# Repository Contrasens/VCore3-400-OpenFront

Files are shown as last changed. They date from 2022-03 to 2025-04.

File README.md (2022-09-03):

# VCore3.0 400mm OpenFront

This is my take at the VCore-3 3D printer from RatRig.

It contains several mods already, the basis is the 400mm VCore-3 from RatRig [https://www.ratrig.com/3d-printing-cnc/3d-printer-kits/all-3d-printer-kits/v-core3configurable.html](https://www.ratrig.com/3d-printing-cnc/3d-printer-kits/all-3d-printer-kits/v-core3configurable.html). The mods I decided to build are: 

* OpenFront Mod: [https://www.thingiverse.com/thing:5140728](https://www.thingiverse.com/thing:5140728)
* Various smaller mods from users of the RatRig community (many thanks to everybody making this great 3D printer an even better one!):
  * [RatRig V-Core 3 Bed Arms heat-set insert mod](https://www.prusaprinters.org/prints/145226-ratrig-v-core-3-bed-arms-heat-set-insert-mod)
  * [RatRig V-Core 3 reinforced and sealed rear motor mount](https://www.printables.com/model/158467-ratrig-v-core-3-reinforced-and-sealed-rear-motor-m)
  * Stronger Pillow Blocks
  * [LGX Lite Fast-Swap-Rigid Gold Series EVA mod](https://www.thingiverse.com/thing:5207408)
  * [Gold Series Rat Rig V-Core 3, XY joiners with clamping mod](https://www.thingiverse.com/thing:4947482)
* ...and my own mods:
  * [My Enclosure](https://www.printables.com/model/270834-enclosure-for-my-ratrig-v-core3-400mm-openfront)
  * [Magnetic holder for PC/Acrylic panels](https://www.printables.com/model/229334-magnetic-holder-for-pcacrylic-panels)
  * [DIN Rail Endcaps for M6x12 Cap Screws](https://www.printables.com/model/152627-din-rail-endcaps-for-m6x12-cap-screws)
  * [DIN Rail Adapter for Meanwell RS-25-5](https://www.printables.com/model/152624-din-rail-adapter-for-meanwell-rs-25-5)
  * [DIN Rail Adapter for Meanwell LRS-200-24 for V-Core3 400](https://www.printables.com/model/152620-din-rail-adapter-for-meanwell-lrs-200-24-for-v-cor)
  * [Fastener for Igus Chain on VCore3](https://www.printables.com/model/145317-fastener-for-igus-chain-on-vcore3)

## How it looks
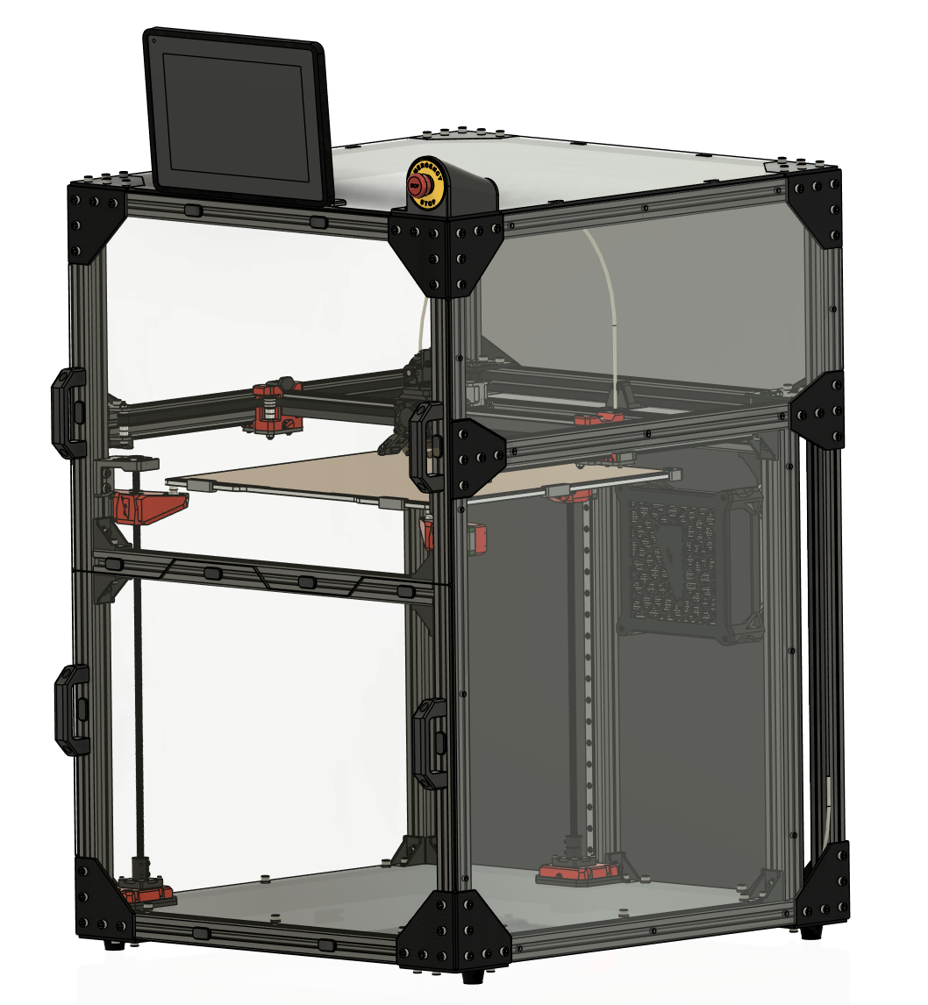
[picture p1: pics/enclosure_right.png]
Enclosure

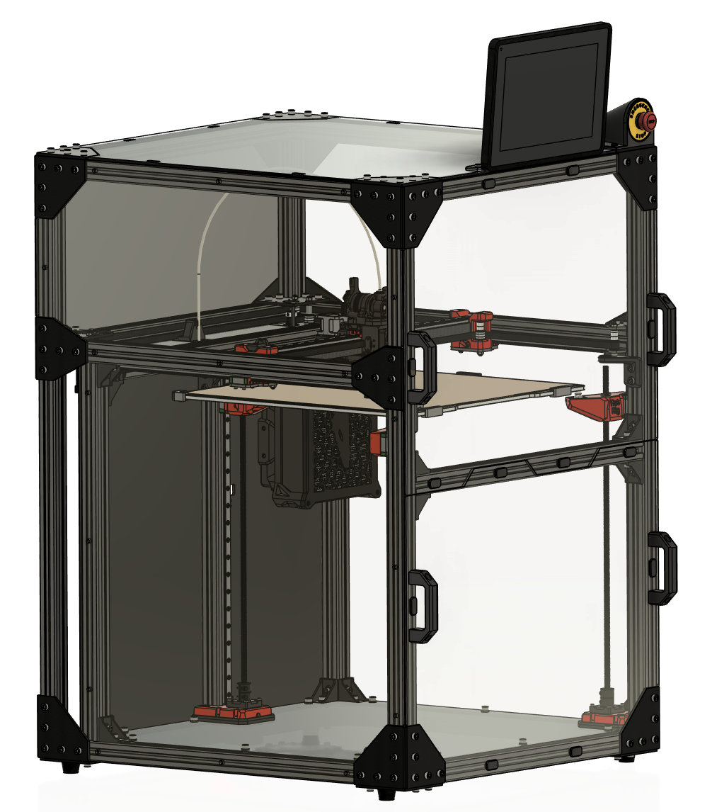
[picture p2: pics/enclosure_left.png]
Enclosure

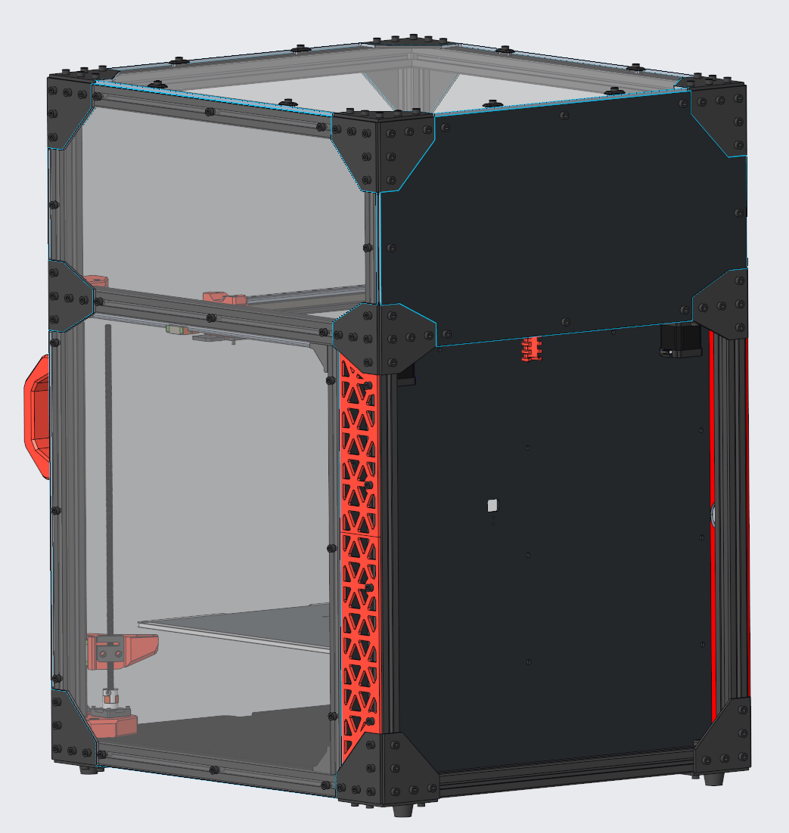
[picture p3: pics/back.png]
Back View

Here is the wiring diagram I will be using. **If you decide to use it, please acknowledge that you are doing this on your own risk!**
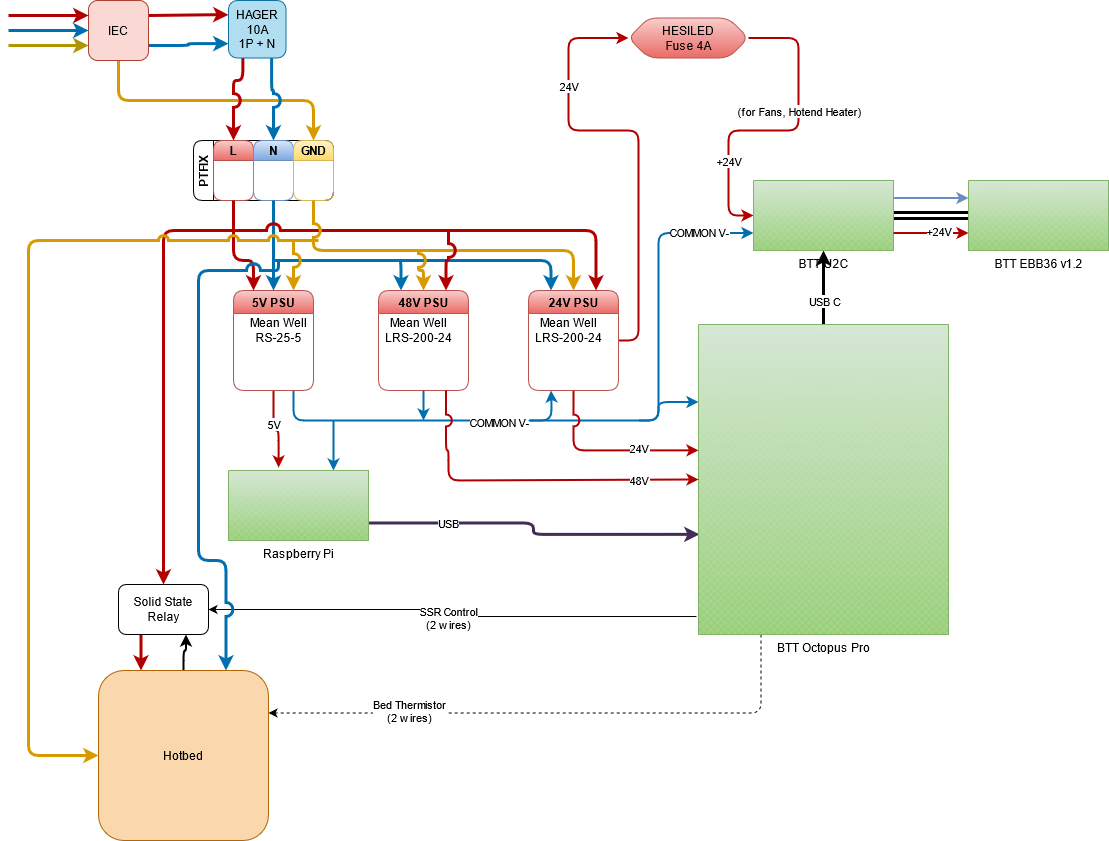
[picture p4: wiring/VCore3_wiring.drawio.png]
Wiring


## Printhead
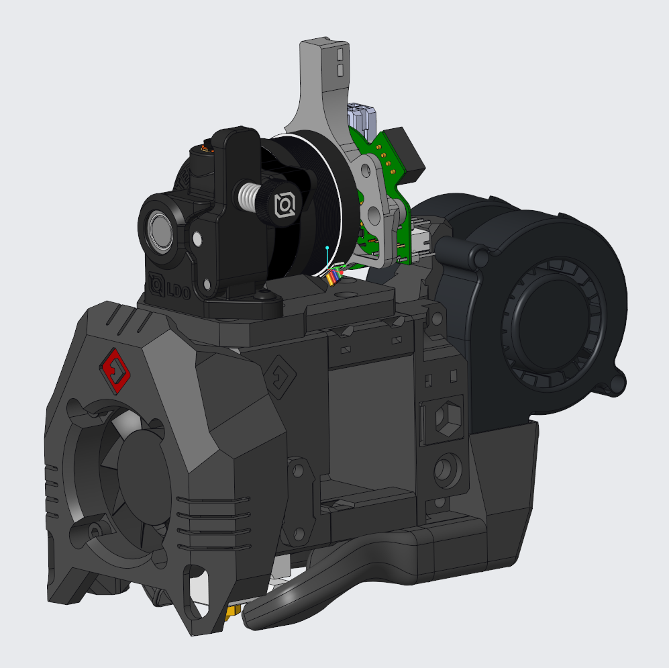
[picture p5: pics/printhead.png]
Printhead


## BOM
Here is my Bill of Material (BOM): [GoogleDrive](https://docs.google.com/spreadsheets/d/1t07DfJ-j9_pQZ918qX5IQbVI45c6goUu2t6Ui3eUhBY/edit?usp=sharing)

## Contact
* [Discord](https://discord.com) user: [Dinu#6139](http://discordapp.com/users/704373657648234526)

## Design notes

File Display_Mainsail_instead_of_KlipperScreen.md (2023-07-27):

# How to switch from using KlipperScreen to Mainsail on the HDMI output of the Raspberry Pi?

## Stop and disable KlipperScreen service
  ```
  sudo systemctl stop KlipperScreen
  sudo systemctl disable KlipperScreen
  ```

## Install Chromium and use the page served by Mainsail in kiosk mode
Read the guidelines (German) available here: [Kiosk Modus auf Touchscreen am Raspberry Pi mit automatischer Anmeldung im Browser](https://smarthomeyourself.de/wiki/raspberrypi/kiosk-modus-auf-touchscreen-am-raspberry-pi-mit-automatischer-anmeldung-im-browser). Basically, you need to do the following (I am just summarizing the steps from the link for future reference in case the content will disappear):

### Raspi Setup 
Disable Overscan compensation
  
  ```
  sudo raspi-config
  2 - Display Options -> D2 - Underscan =>> NO (DISABLE overscan compensation)
  ```
Enable Auto-login
  ```
  sudo raspi-config
  1 - System Options -> S5 – Boot / Auto Login =>> B2 – Console Autologin
  ```

### Install Necessary Packets
Update Raspbian
```
sudo apt update
sudo apt upgrade
```
Install X11 server and the Chromium browser
```
sudo apt-get install --no-install-recommends xserver-xorg x11-xserver-utils xinit openbox xdotool
sudo apt-get install --no-install-recommends chromium-browser
```

### Configure Autostart
```
sudo nano /etc/xdg/openbox/autostart
```
In the file, add the following (when finished, close & save with Ctrl+X):
```
xset -dpms            # turn off display power management system
xset s noblank        # turn off screen blanking
xset s off            # turn off screen saver

# Remove exit errors from the config files that could trigger a warning
sed -i 's/"exited_cleanly":false/"exited_cleanly":true/' ~/.config/chromium/'Local State'
sed -i 's/"exited_cleanly":false/"exited_cleanly":true/; s/"exit_type":"[^"]\+"/"exit_type":"Normal"/' ~/.config/chromium/Default/Preferences

# Run Chromium in kiosk mode
chromium-browser  --noerrdialogs --check-for-update-interval=31536000 --disable-infobars --kiosk $KIOSK_URL &
```

### Set the Home Address to be opened in the Browser
```
sudo nano /etc/xdg/openbox/environment
```
In the file, add the following (when finished, close & save with Ctrl+X):
```
  export KIOSK_URL=http://127.0.0.1
```

### Start xserver (without showing the cursor)
```
sudo nano ~/.bash_profile
```
In the file, add the following (when finished, close & save with Ctrl+X):
```
[[ -z $DISPLAY && $XDG_VTNR -eq 1 ]] && startx -- -nocursor
```

### Automatically login into the browser after boot
```
sudo nano /etc/xdg/openbox/autostart
```
Add the following at the end of the file (when finished, close & save with Ctrl+X):
```
sleep 30
exec /home/pi/start_ha.sh
```
Now, create the start_ha.sh file (a shell script):
```
sudo nano /home/pi/start_mainsail.sh
```
In the file, add the following (when finished, close & save with Ctrl+X):
```
# login to Mainsail (not necessary?)
sleep 30
export XAUTHORITY=/home/pi/.Xauthority; export DISPLAY=:0; xdotool type YOUR_MAINSAIL_USERNAME
sleep 1;
export XAUTHORITY=/home/pi/.Xauthority; export DISPLAY=:0; xdotool key Tab
sleep 1;
export XAUTHORITY=/home/pi/.Xauthority; export DISPLAY=:0; xdotool type YOUR_MAINSAIL_PASSWORD

sleep 1;
export XAUTHORITY=/home/pi/.Xauthority; export DISPLAY=:0; xdotool key Return
sleep 5;

# click save login-button
export XAUTHORITY=/home/pi/.Xauthority; export DISPLAY=:0; xdotool mousemove 1835 1030;
sleep 1;
export XAUTHORITY=/home/pi/.Xauthority; export DISPLAY=:0;xdotool click 1;
sleep 2;
```
Change the rights of the newly created file to be executable:
```
sudo chmod +x /home/pi/start_ha.sh
```
Reboot, and enjoy!
```
sudo reboot now
```

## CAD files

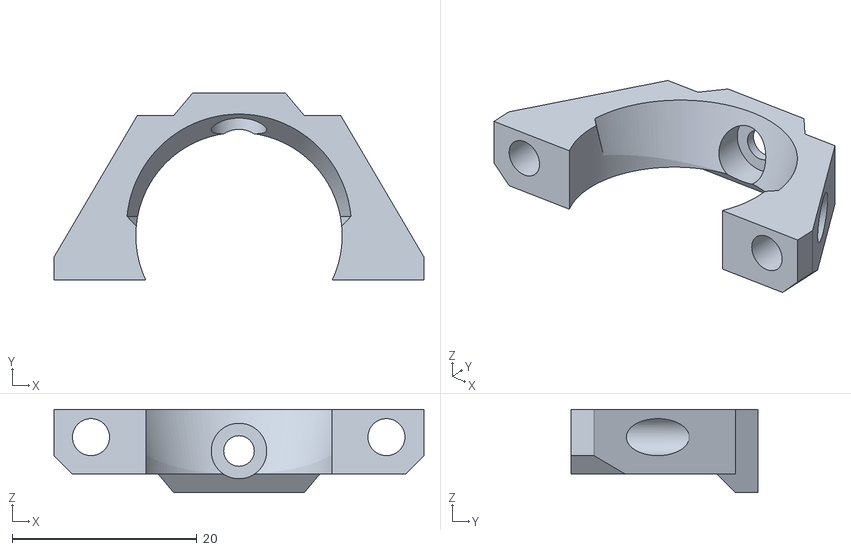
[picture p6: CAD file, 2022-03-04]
cad/_PRINTED_/EVA2.4.0/black/Dragon_heatsink_support.stl
40.0 x 20.2 x 9.00

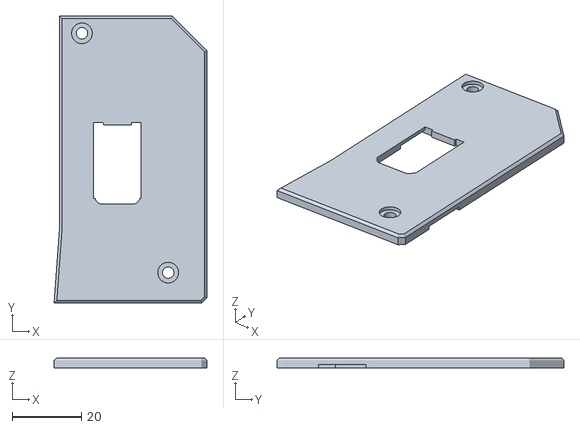
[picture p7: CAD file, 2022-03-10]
cad/_PRINTED_/extra/black/sabre_holder_top.stl
44.2 x 83.0 x 3.00

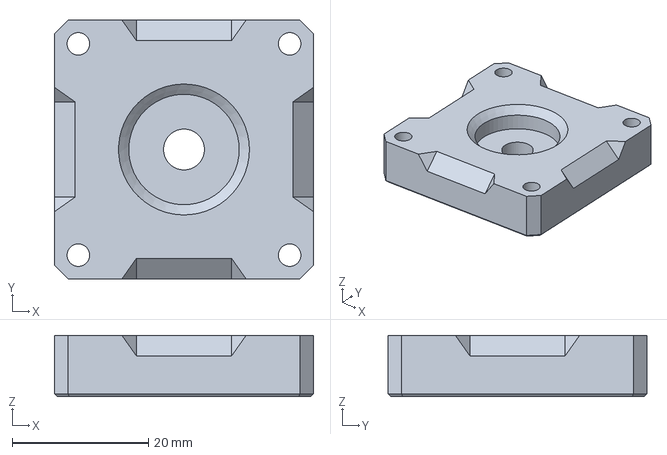
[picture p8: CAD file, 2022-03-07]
cad/_PRINTED_/printed_parts/essentials/black/pillow_block_lower.step
38.0 x 38.0 x 9.00 mm

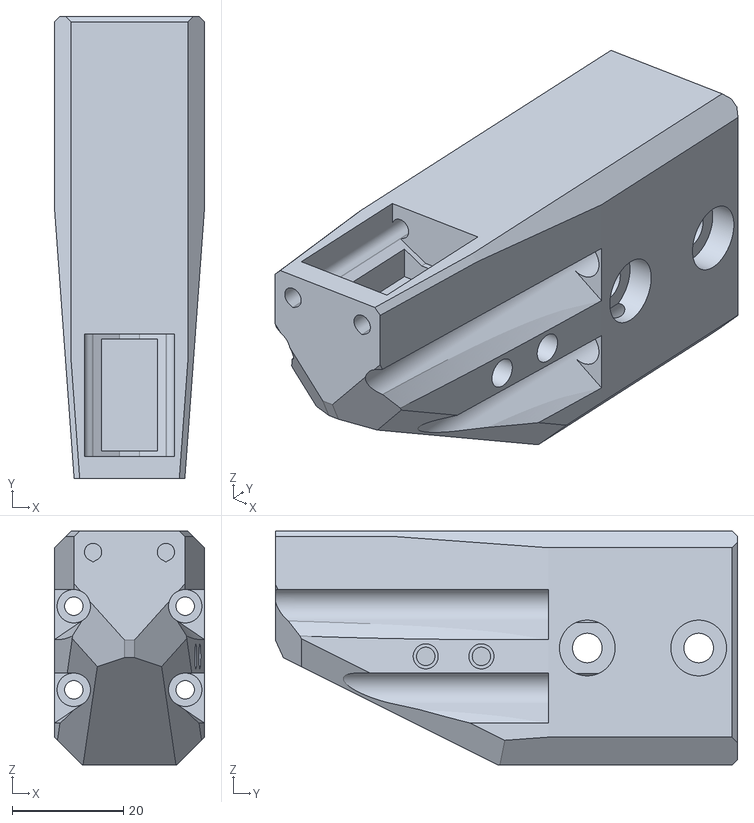
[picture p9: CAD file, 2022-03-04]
cad/_PRINTED_/printed_parts/essentials/red/V-Core-heat-inset_bed_arm_back.stl
27.0 x 83.0 x 42.0

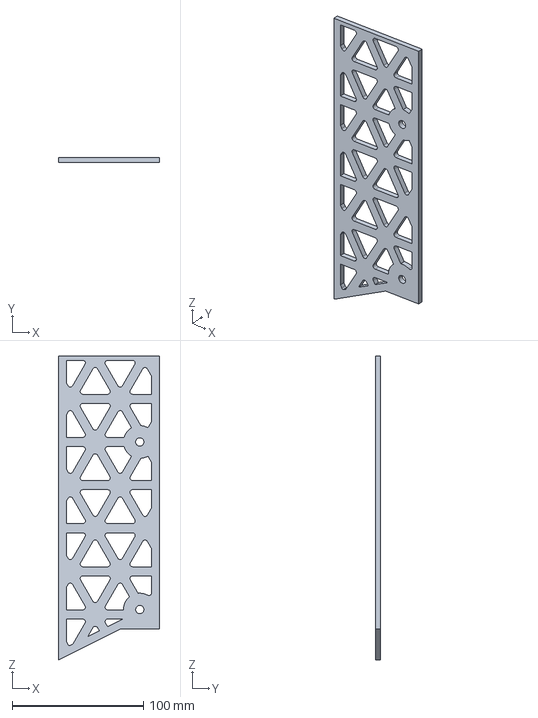
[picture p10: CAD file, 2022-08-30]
cad/Enclosure/Meshes/side_mesh_right_top.stp
77.0 x 4.00 x 232.0 mm

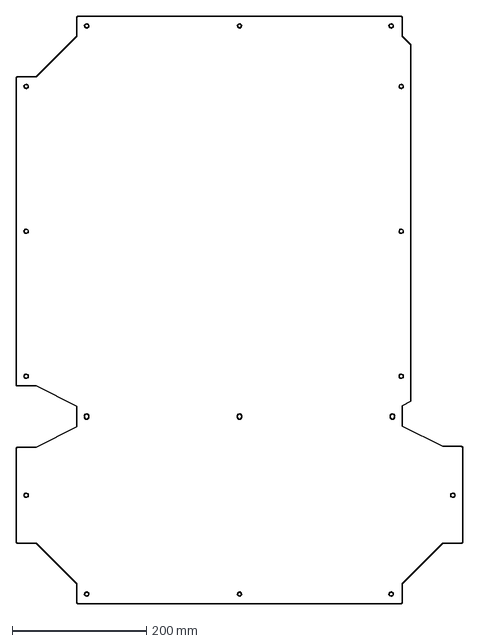
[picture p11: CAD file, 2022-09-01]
cad/Enclosure/Panels/DXF/side-panel_PC4mm_2X.dxf
664.0 x 874.0 mm

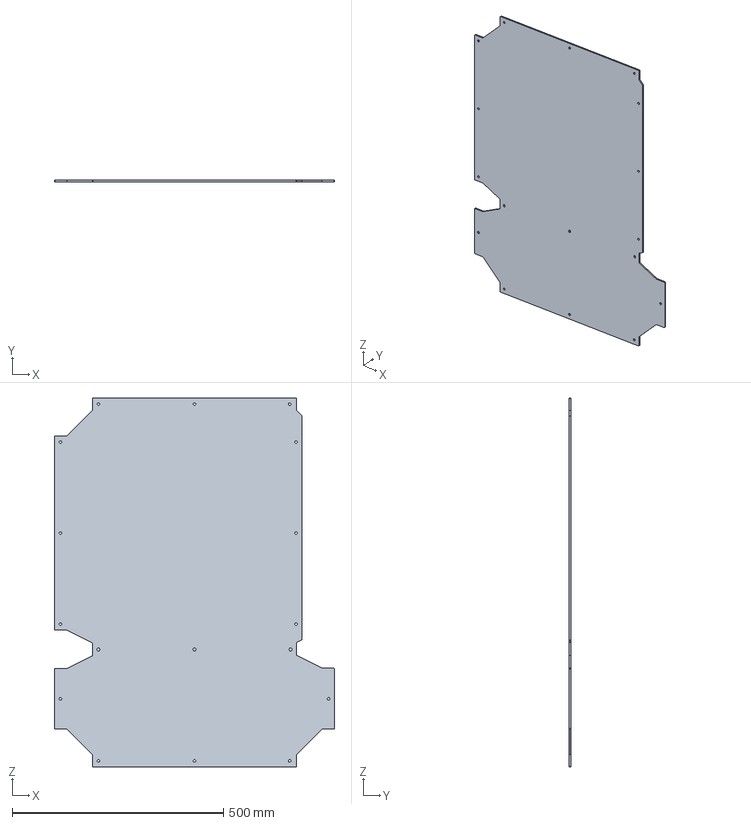
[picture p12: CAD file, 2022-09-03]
cad/Enclosure/Panels/STEP/side-panel.stp
664.0 x 4.00 x 874.0 mm

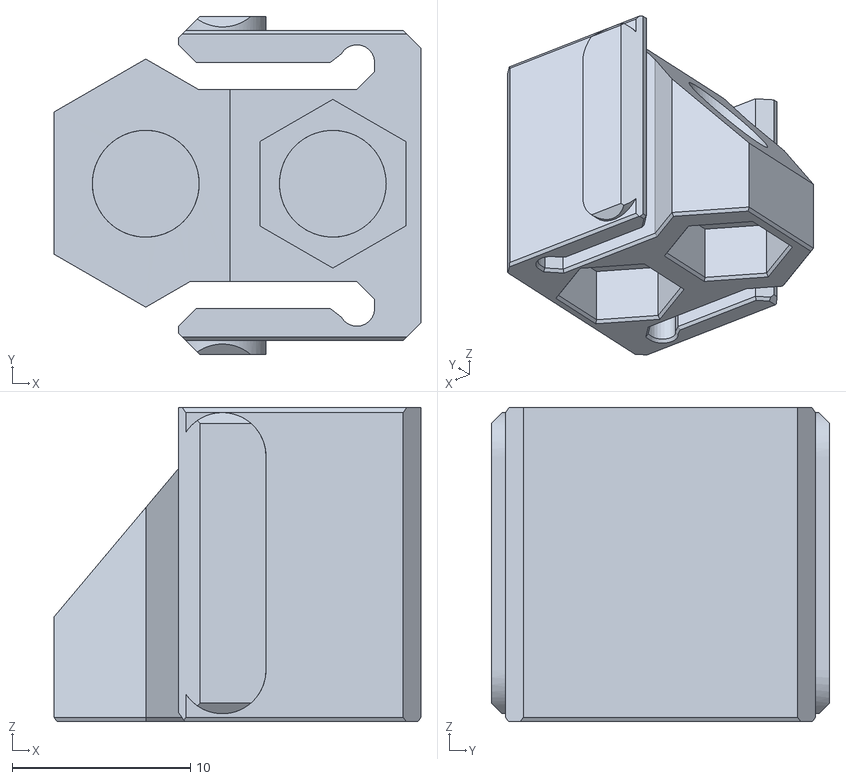
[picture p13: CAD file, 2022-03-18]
cad/Extras/Carbon Tube Adapter/x-tube_nuts.stl
20.6 x 19.0 x 17.6

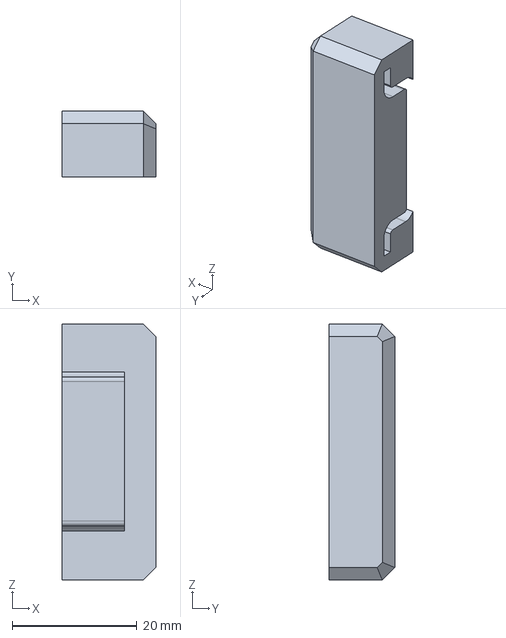
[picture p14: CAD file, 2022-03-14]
cad/Extras/DIN Rail Adapters/DIN Rail Endcaps/din_rail-end.stp
15.0 x 10.5 x 41.0 mm

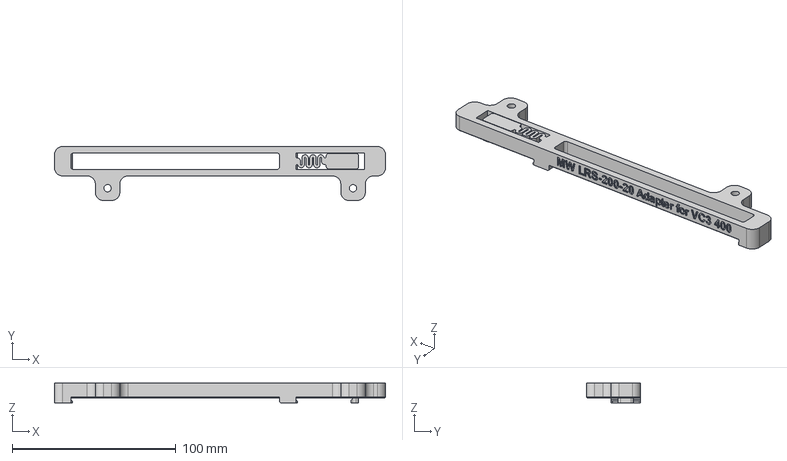
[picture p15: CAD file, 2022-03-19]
cad/Extras/DIN Rail Adapters/MeanWell LRS-200-24/lrs-200-24_din_adapter_v3.step
202.3 x 33.0 x 12.0 mm

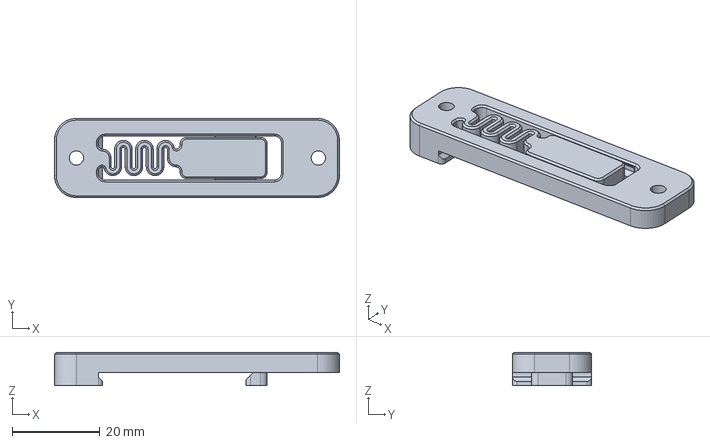
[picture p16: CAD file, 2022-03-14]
cad/Extras/DIN Rail Adapters/MeanWell RS-25-5/rs-25-5_din_adapter.stp
64.8 x 18.0 x 7.60 mm

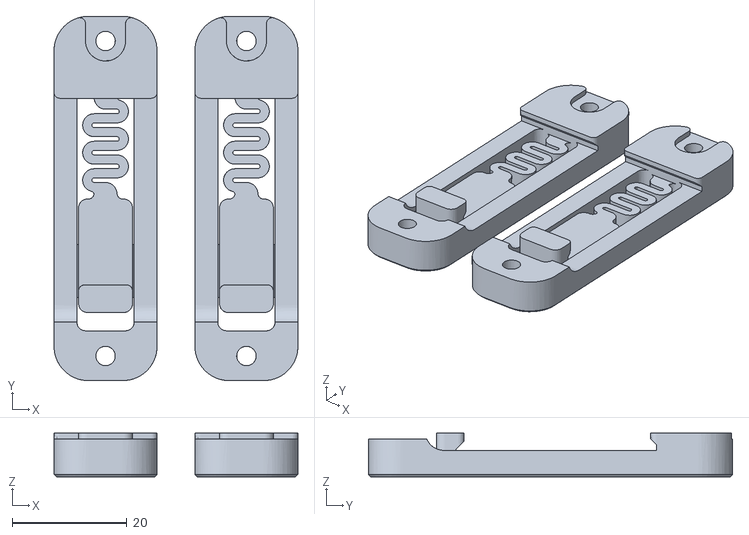
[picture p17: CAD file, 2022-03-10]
cad/Extras/DIN Rail Adapters/Octopus_Raspi_mount/DIN_Support_X2.stl
42.6 x 63.6 x 7.60

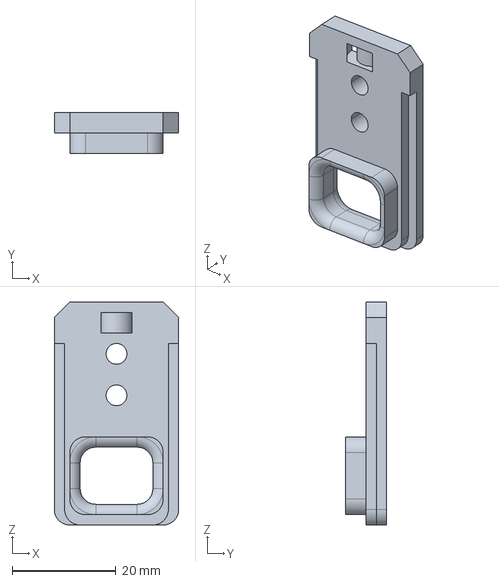
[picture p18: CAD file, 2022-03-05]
cad/Extras/Igus Chain/befestigung_igus_kette.stp
24.0 x 8.00 x 43.0 mm

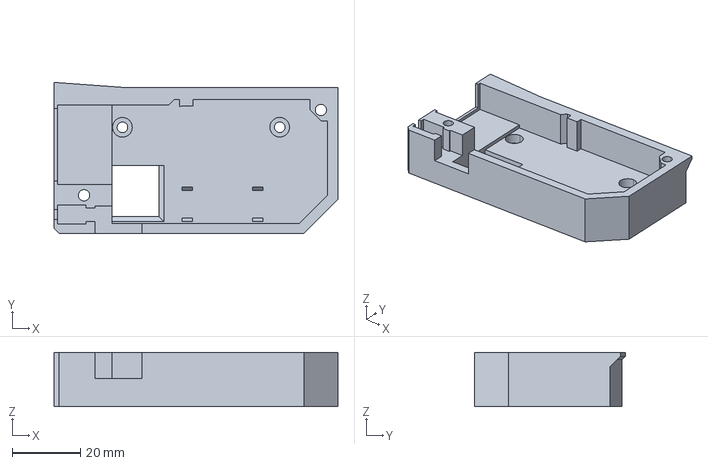
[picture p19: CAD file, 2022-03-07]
cad/Extras/Igus Chain/Jevermeister/sabre_holder.stp
83.0 x 44.2 x 15.8 mm

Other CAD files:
cad/Mods/EVA_2_4_0_LGXLite_Dragon_Inserts/[Face] Universal - universal_face.stl
cad/Mods/EVA_2_4_0_LGXLite_Dragon_Inserts/Addons/top_endstop_angled.stl
cad/Mods/Jevermeister/Bed Arms Heat Inserts/V-Core-heat-inset_bed_arm_back.step
cad/Mods/Jevermeister/EVA Toolboard Holder/eva_toolboard_cable_relief v1.stl
MM_Prints/RR_Disk.3mf
My_SS_Profiles/ratrig-vcore-bed-400x400.stl
cad/Enclosure/Accesories/3030_handle.stp
cad/Enclosure/Accesories/magnet_holder_1_magnet.step
cad/Enclosure/Accesories/magnet_holder_2_magnets.step
cad/Enclosure/Accesories/screw_holder.stp
cad/Enclosure/Meshes/side_mesh_right_bottom.stp
cad/Enclosure/Panels/DXF/back-panel_DIBOND.dxf
cad/Enclosure/Panels/DXF/front-panel_PC4mm.dxf
cad/Enclosure/Panels/DXF/side-panel_PC4_2X.dxf
cad/Enclosure/Panels/DXF/side-panel_X2_PC4mm.dxf
cad/Enclosure/Panels/DXF/top-panel_PC4mm.dxf
cad/Enclosure/Panels/STEP/back-panel.stp
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

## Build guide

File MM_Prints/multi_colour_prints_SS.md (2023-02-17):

# How to set-up SuperSlicer to work with multi-colour material

## Prerequisites
- SuperSlicer (tested with: v2.4.58.4, v2.4.58.5, v2.5.59.0 and nightly v2.5.59.2)
- Expert settings enabled

## HowTo Step-by-step
1. Printer Settings 
   - General -> Capabilities -> Extruders = 2
   - General -> Capabilities -> Single Extruder Multi Material = True
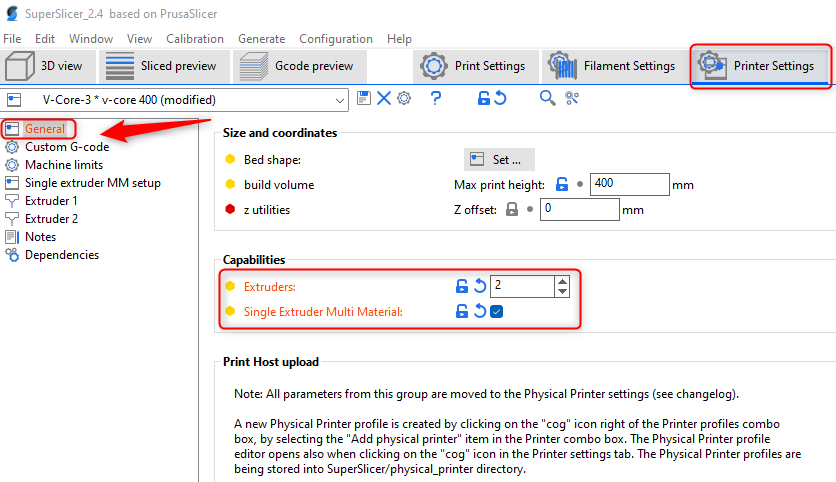
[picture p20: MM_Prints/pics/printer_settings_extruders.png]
Printer Settings
 

1. **Save & Restart SuperSlicer**
 
2. Printer Settings, set all Single extruder multimaterial parameters to 0:
   
   - General -> Use relative E distances = enable
   - Custom G-code -> Tool change g-code: add "PAUSE" (without the ")
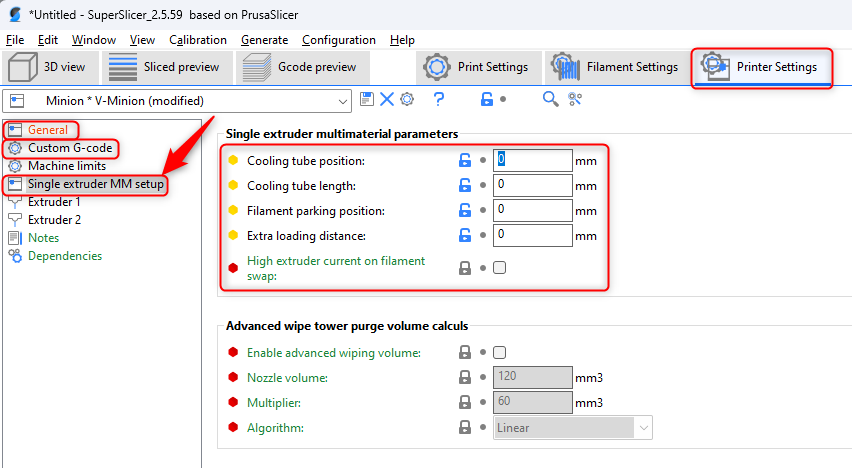
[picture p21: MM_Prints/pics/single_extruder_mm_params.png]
Single Extruder
 

 1. Filament settings
      - Multimaterial settings -> Wipe tower parameters -> Minimal purge on wipe tower = 200 for V6 and 500 for Volcano
      - Multimaterial settings -> Wipe tower parameters -> Max speed on the wipe tower = 300%
      - Multimaterial settings -> Toolchange parameters with single extruder MM printers -> Number of cooling moves = 0
      - Multimaterial settings -> Toolchange parameters with single extruder MM printers -> Ramming parameters
        - Turn off all Ramming settings:
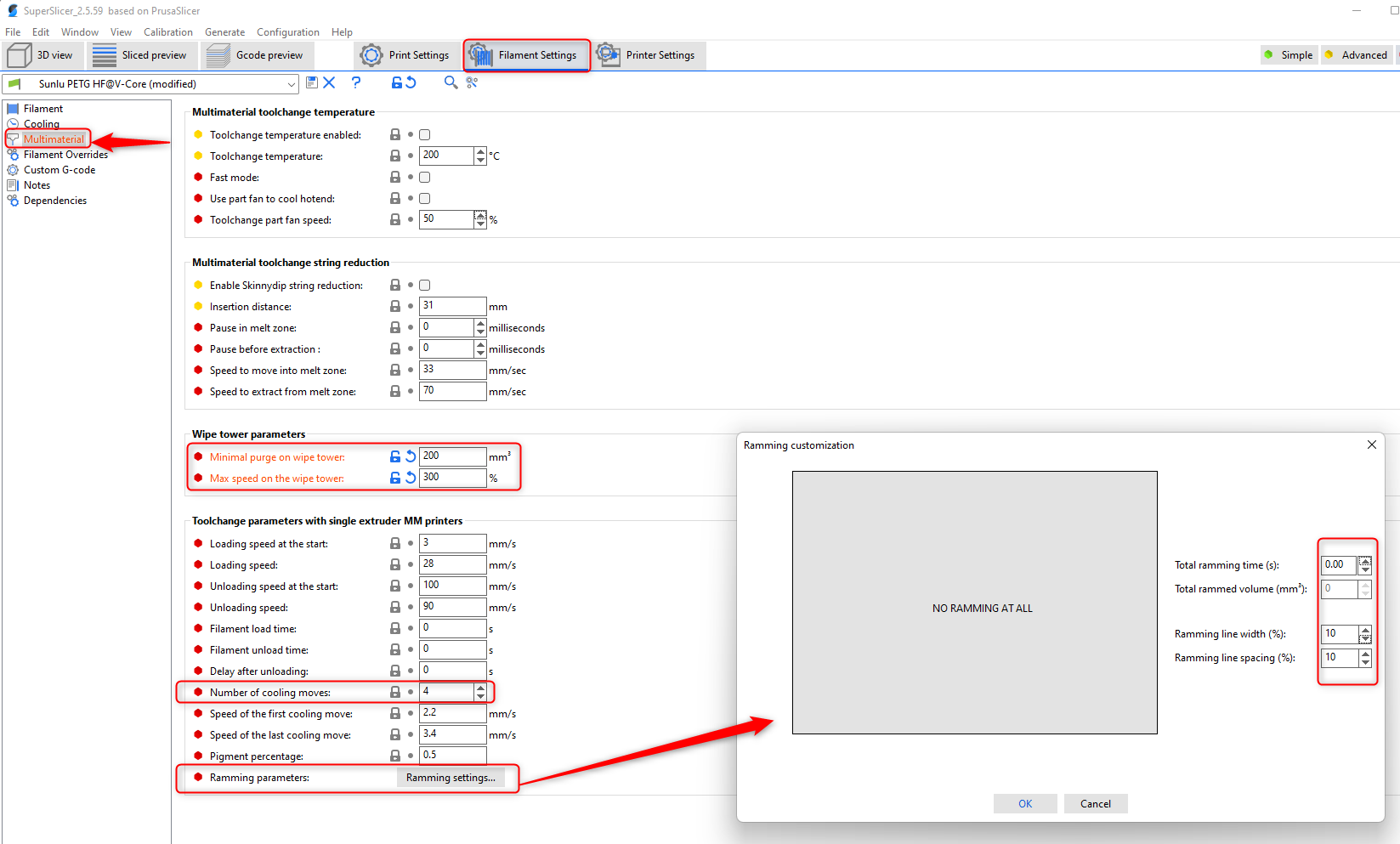
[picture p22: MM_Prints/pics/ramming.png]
Deactivate ramming
          
 2. Print settings
      - Multiple extruders -> wipe tower = enable
      - Multiple extruders -> wipe tower -> "Prime all printing extruders" is not set
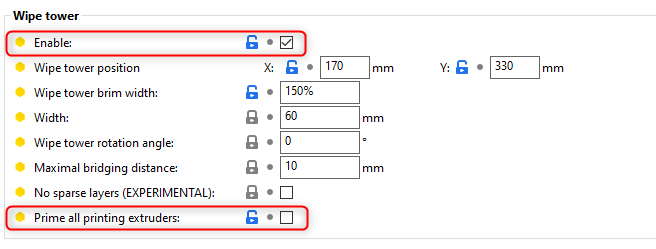
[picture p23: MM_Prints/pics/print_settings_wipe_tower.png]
Wipe Tower settings
        

## How to slice the objects with different colours
- The object that need to be printed in several colours must be made out of several smaller objects, for each colour a separate one, so first split the object
- Import all of the objects in SuperSlicer: first the base object, then right click it -> Add part -> Load
  
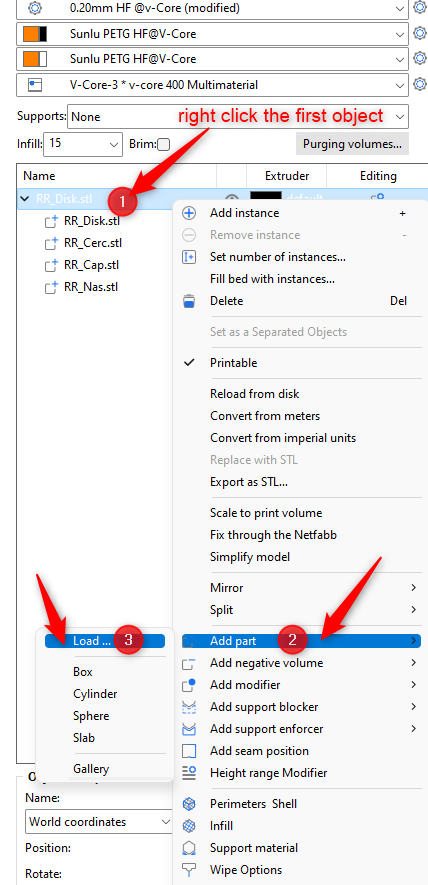
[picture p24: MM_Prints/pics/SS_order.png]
SS Order
  
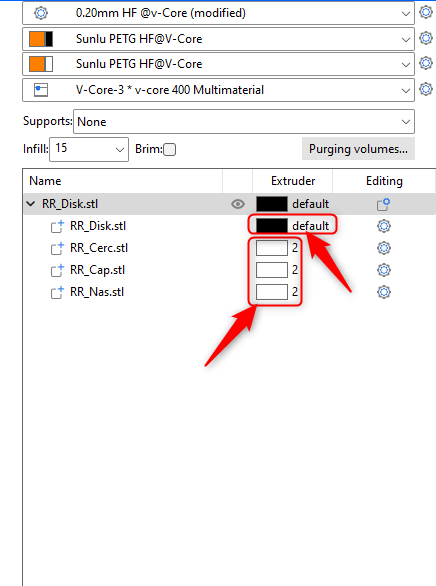
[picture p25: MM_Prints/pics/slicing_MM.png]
Slicing
  
  
- Associate them with different extruders
- Slice it and start the print
- When the print pauses, swap the filament and then click resume

## Example 
You can use this example SS Project: [RR_Disk.3mf](RR_Disk.3mf)

## Special Thanks:
Helge Keck for writing the initial version for the RatRig Discord Community

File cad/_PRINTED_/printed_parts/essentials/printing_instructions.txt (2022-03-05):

https://v-core.ratrig.com/printed_parts/#printing-instructions

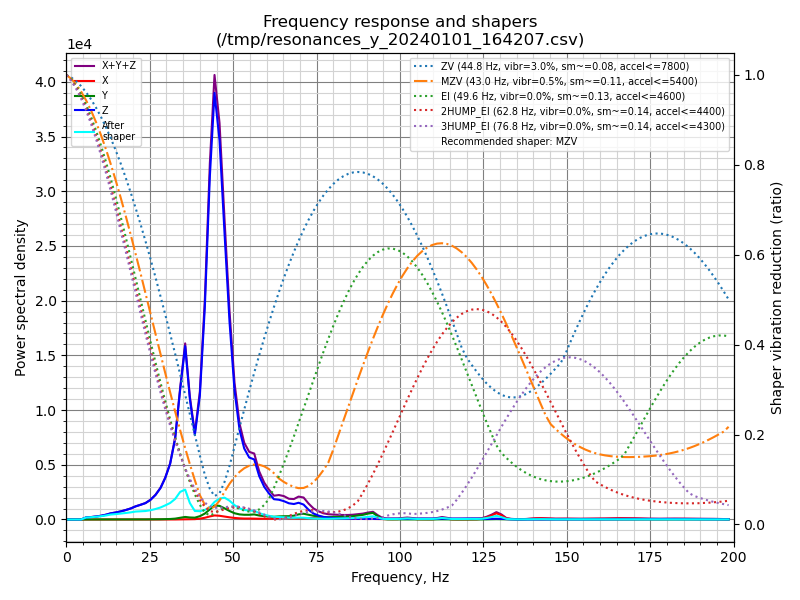
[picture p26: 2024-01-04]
printer_data/ratos_2_0_config/input_shaper/resonances_y_2024-01-01-164435.png

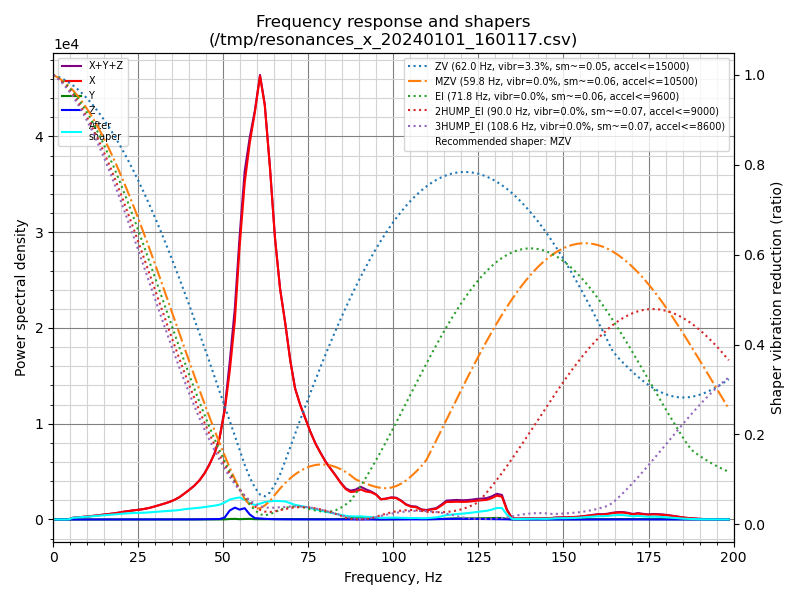
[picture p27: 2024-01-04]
printer_data/ratos_2_0_config/input_shaper/resonances_x_2024-01-01-160543.png

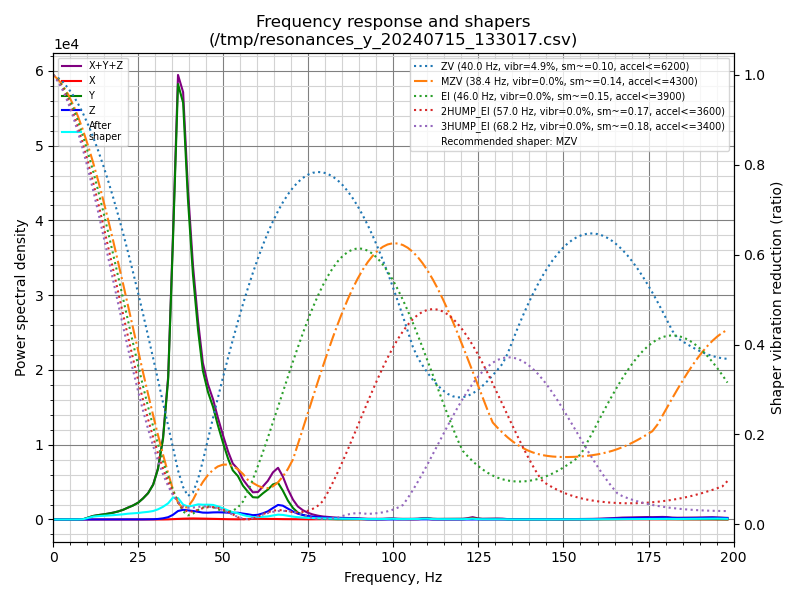
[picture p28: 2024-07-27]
printer_data/ratos_2_1_config/input_shaper/input_shaper/resonances_y_2024-07-15-133238.png

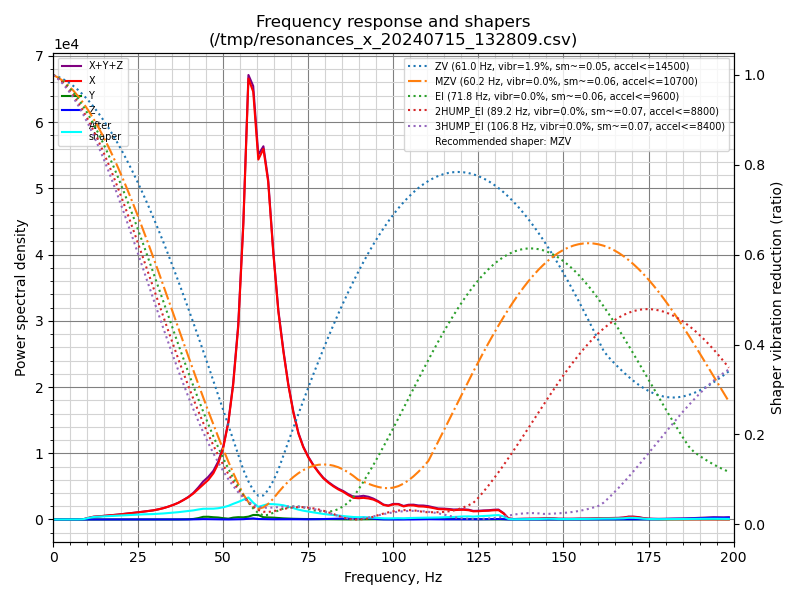
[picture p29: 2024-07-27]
printer_data/ratos_2_1_config/input_shaper/input_shaper/resonances_x_2024-07-15-133224.png

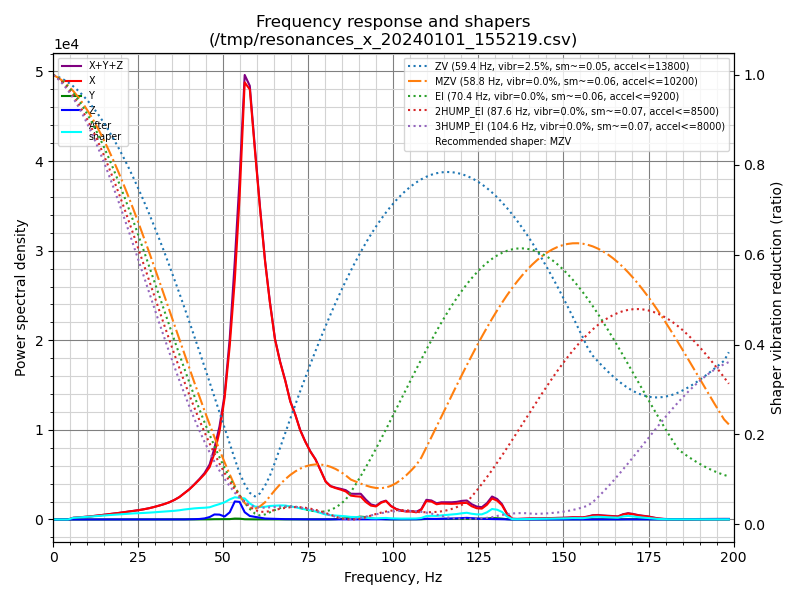
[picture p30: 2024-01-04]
printer_data/ratos_2_0_config/input_shaper/resonances_x_2024-01-01-155646.png

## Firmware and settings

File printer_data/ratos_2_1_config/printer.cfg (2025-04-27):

#############################################################################################################
### CONFIGURATION GENERATED BY THE RATOS CONFIGURATOR
#############################################################################################################
#[include RatOS.cfg]  # this is the unmodified RaatOS configuration
[include RatOS_modified.cfg]

#############################################################################################################
### MACRO CONFIGURATION
### Configure the behavior of RatOS macros
### See: https://os.ratrig.com/docs/configuration/macros
#############################################################################################################
[gcode_macro RatOS]
variable_relative_extrusion: False
variable_preheat_extruder: True
variable_calibrate_bed_mesh: True
variable_nozzle_priming: "primeblob"
variable_start_print_park_in: "back"
variable_start_print_park_z_height: 50
variable_end_print_park_in: "back"
variable_pause_print_park_in: "back"
variable_macro_travel_speed: 600
variable_macro_travel_accel: 8000
# Euclid macros
variable_stowable_probe_position_preflight: [ 27, 30 ]
variable_stowable_probe_position_side:      [ 27, 0  ]
variable_stowable_probe_position_dock:      [  7, 0  ]
variable_stowable_probe_position_exit:      [  7, 30 ]
# Adaptive meshing
variable_adaptive_mesh: True

#############################################################################################################
### USER OVERRIDES & CUSTOM CONFIGURATION
### Anything custom you want to add, or RatOS configuration you want to override, do it here.
### This section is pre-populated with the most common settings you may want to change.
### See: https://os.ratrig.com/docs/configuration/includes-and-overrides
###
### It is recommended that you follow these steps to properly calibrate your printer:
### 0) Sanity check and PID Tuning: https://www.klipper3d.org/Config_checks.html
### 1) Z-offset calibration: https://www.klipper3d.org/Probe_Calibrate.html#calibrating-probe-z-offset
### 2) Pressure Advance: https://www.klipper3d.org/Pressure_Advance.html
### 3) Skew Correction: https://www.klipper3d.org/Skew_Correction.html
### 4) Resonance Compensation: https://www.klipper3d.org/Resonance_Compensation.html
### RatOS has dedicated macro's to generate shaper graphs for deeper analysis (requires accelerometer).
### Use MEASURE_COREXY_BELT_TENSION to compare tension between belts, and use
### GENERATE_SHAPER_GRAPHS to generate the resonance graphs for analysing and manually entering input shaper
### configuration.
### You can run SHAPER_CALIBRATE to automatically calibrate your input shaper configuration, if you just want
### to get started.
### Additionally, you can use the Realtime Analysis Tool to analyze your printer's performance in real-time.
### Read more about klipper here: https://www.klipper3d.org/Overview.html
#############################################################################################################

#---------------------------------------------------- X -----------------------------------------------------
# The A motor in the CoreXY system, located at the rear left of the printer
# Connected to MOTOR 0 on Octopus Pro 446
#------------------------------------------------------------------------------------------------------------
[stepper_x]
dir_pin: !x_dir_pin                 # Add ! in front of pin name to reverse the direction of stepper_x
rotation_distance: 40              # 40 for 20 tooth 2GT pulleys, 32 for 16 tooth 2GT pulleys
homing_speed: 50
position_min: 0
position_max: 400
position_endstop: 0

#---------------------------------------------------- Y -----------------------------------------------------
# The B motor in the CoreXY system, located at the rear right of the printer
# Connected to MOTOR 1 on Octopus Pro 446
#------------------------------------------------------------------------------------------------------------
[stepper_y]
dir_pin: !y_dir_pin                 # Add ! in front of pin name to reverse the direction of stepper_y
rotation_distance: 40              # 40 for 20 tooth 2GT pulleys, 32 for 16 tooth 2GT pulleys
homing_speed: 50
position_min: 0
position_max: 400
position_endstop: 400

#---------------------------------------------------- Z -----------------------------------------------------
# The left Z motor for the kinematic bed
# Connected to MOTOR 5 on Octopus Pro 446
#------------------------------------------------------------------------------------------------------------
[stepper_z]
dir_pin: !z0_dir_pin               # Remove ! in front of pin name to reverse the direction of stepper_z
rotation_distance: 4               # 4 for TR8*4 lead screws
homing_speed: 10
position_min: -5
position_max: 400

#---------------------------------------------------- Z1 ----------------------------------------------------
# The rear Z motor for the kinematic bed
# Connected to MOTOR 6 on Octopus Pro 446
#------------------------------------------------------------------------------------------------------------
[stepper_z1]
dir_pin: !z1_dir_pin               # Remove ! in front of pin name to reverse the direction of stepper_z1
rotation_distance: 4               # 4 for TR8*4 lead screws

#---------------------------------------------------- Z2 ----------------------------------------------------
# The right Z motor for the kinematic bed
# Connected to MOTOR 7 on Octopus Pro 446
#------------------------------------------------------------------------------------------------------------
[stepper_z2]
dir_pin: !z2_dir_pin               # Remove ! in front of pin name to reverse the direction of stepper_z2
rotation_distance: 4               # 4 for TR8*4 lead screws

#------------------------------------------------- EXTRUDER -------------------------------------------------
# The extruder motor used for pushing filament through the toolhead
# Connected to EBB36 v1.2
#------------------------------------------------------------------------------------------------------------
[extruder]
dir_pin: toolboard_t0:e_dir_pin   # Remove ! in front of pin name to reverse the direction of extruder
rotation_distance: 4.63            # Orbiter 2 default
#pressure_advance: 0.05            # Check https://www.klipper3d.org/Pressure_Advance.html for pressure advance tuning.
#control: pid
#pid_kp: 28.413
#pid_ki: 1.334
#pid_kd: 151.300


[heater_bed]
#control: pid
#pid_Kp: 22.2
#pid_Ki: 1.08
#pid_Kd: 114

# Probe configuration
[probe]
#z_offset: 11.330 # Will be commented out after a successful PROBE_CALIBRATE and SAVE_CONFIG
pin: ^toolboard_t0:probe_pin# For NPN NC probes such as the Super Pinda / Vinda / SupCR / Decoprobe probes.
#pin: ^!toolboard_t0:probe_pin # NPN NO (refer to the specs of your probe)
#pin: toolboard_t0:probe_pin # PNP NO (refer to the specs of your probe)
#pin: !toolboard_t0:probe_pin # PNP NC (refer to the specs of your probe)


#############################################################################################################
### USER OVERRIDES
### Anything custom you want to add, or RatOS configuration you want to override, do it here.
#############################################################################################################

[mcu toolboard_t0]
canbus_uuid: 2263dd046341    #v1.2 EBB36
canbus_interface: can0

[bed_mesh]
horizontal_move_z: 15

[fan]
shutdown_speed: 0
kick_start_time: 0.3   #Time (in seconds) to run the fan at full speed when either first enabling or increasing it by more than 50% 
cycle_time: 0.01

[input_shaper]
shaper_type_x = mzv
shaper_freq_x = 59.8
shaper_type_y = mzv
shaper_freq_y = 37.6

#############################################################################################################
### Exclude objects
### https://docs.mainsail.xyz/overview/features/exclude-objects
#############################################################################################################
[exclude_object]


#############################################################################################################
### Enclosure PTC heater 300W
### 
#############################################################################################################
[temperature_sensor Enclosure_Top]
sensor_type: Generic 3950
sensor_pin: PF4

[heater_generic chamber]
heater_pin: PB10
max_power: 0.75   #max 75% PWM
sensor_type: Generic 3950
sensor_pin: PF7
control: watermark
max_delta: 1.0
min_temp: -100
max_temp: 105
gcode_id: D

[verify_heater chamber]
max_error: 120
check_gain_time: 20
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

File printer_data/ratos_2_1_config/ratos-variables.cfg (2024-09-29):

[Variables]
idex_applied_offset = 1
idex_xcontrolpoint = 200
idex_xoffset = 0.0
idex_ycontrolpoint = 50
idex_yoffset = 0.0
idex_zcontrolpoint = 50
idex_zoffset = 0.0
idex_zoffsetcontrolpoint = 25
nozzle_expansion_applied_offset = 0
nozzle_expansion_coefficient_t0 = 0.06
nozzle_expansion_coefficient_t1 = 0.06
t0_filament = ('unknown', 'unknown', 220)

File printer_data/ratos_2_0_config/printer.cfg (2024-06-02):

# Rat Rig V-core 3 Klipper Config
# Documentation: https://os.ratrig.com

# The first thing you'll need to do is go through this file and comment out / uncomment
# the files and/or settings you need.
# You'll be able to print just fine with this config as it is, but it is recommended
# that you follow these steps to properly calibrate your printer:
# 0) Sanity check and PID Tuning: https://www.klipper3d.org/Config_checks.html
# 1) Pressure Advance: https://www.klipper3d.org/Pressure_Advance.html
# 2) Skew Correction: https://www.klipper3d.org/Skew_Correction.html
# 3) Resonance Compensation: https://www.klipper3d.org/Resonance_Compensation.html

# Read more about klipper here: https://www.klipper3d.org/Overview.html

#############################################################################################################
### CONTROL BOARD
### Pick the board you have installed and wired in your printer.
#############################################################################################################
#[include RatOS/boards/btt-skr-pro-12/config.cfg]
#[include RatOS/boards/btt-octopus-11/config.cfg]
#[include RatOS/boards/btt-octopus-11-407/config.cfg]
[include RatOS/boards/btt-octopus-pro-446/config.cfg]
#[include RatOS/boards/btt-octopus-pro-429/config.cfg]
#[include RatOS/boards/btt-octopus-pro-h723/config.cfg]
#[include RatOS/boards/btt-manta-m8p/config.cfg]
#[include RatOS/boards/fysetc-spider/config.cfg]

#############################################################################################################
### BASE SETUP
#############################################################################################################
[include RatOS/printers/v-core-3/v-core-3.cfg]
[include RatOS/homing.cfg]
[include RatOS/macros.cfg]
[include RatOS/shell-macros.cfg]
[include RatOS/printers/v-core-3/macros.cfg]

#############################################################################################################
### STEPPER MOTORS, DRIVERS & SPEED LIMITS
### Pick the drivers and stepper motors you're using. See the RatOS documentation for custom combinations.
#############################################################################################################
[include RatOS/printers/v-core-3/steppers.cfg]

# UNCOOLED TMC 2209 + LDO-42STH48-2504AC
#[include RatOS/printers/v-core-3/tmc2209.cfg]
#[include RatOS/printers/v-core-3/speed-limits-basic.cfg]
#[include RatOS/steppers/ldo/42sth48-2504ac/2209/24v-1.1a-x.cfg]
#[include RatOS/steppers/ldo/42sth48-2504ac/2209/24v-1.1a-y.cfg]
#[include RatOS/steppers/ldo/42sth48-2504ac/2209/24v-1.1a-z.cfg]
#[include RatOS/steppers/ldo/42sth48-2504ac/2209/24v-1.1a-z1.cfg]
#[include RatOS/steppers/ldo/42sth48-2504ac/2209/24v-1.1a-z2.cfg]

# COOLED TMC 2209 + LDO-42STH48-2504AC
# This increases motor torque, positional accuracy and speed limits.
# don't enable this before your printer is fully configured and you have a fan blowing on your stepper drivers.
#[include RatOS/printers/v-core-3/speed-limits-performance.cfg]
#[include RatOS/printers/v-core-3/tmc2209-performance.cfg]
#[include RatOS/steppers/ldo/42sth48-2504ac/2209/24v-1.6a-x.cfg]
#[include RatOS/steppers/ldo/42sth48-2504ac/2209/24v-1.6a-y.cfg]
#[include RatOS/steppers/ldo/42sth48-2504ac/2209/24v-1.6a-z.cfg]
#[include RatOS/steppers/ldo/42sth48-2504ac/2209/24v-1.6a-z1.cfg]
#[include RatOS/steppers/ldo/42sth48-2504ac/2209/24v-1.6a-z2.cfg]

# STEALTH MODE (Enables stealthchop and limits velocity and acceleration)
# NOTE: You still need to include one of the above stepper motor definitions.
# NOTE: This will make your printer quiter but less accurate, it's an inherent side effect of stealthchop.
#[include RatOS/printers/v-core-3/speed-limits-stealth.cfg]
#[include RatOS/printers/v-core-3/tmc2209-stealth.cfg]

#############################################################################################################
### PHYSICAL DIMENSIONS
### Pick your printer size
#############################################################################################################
# Remove the # from your printer size below.
# Similarly add a # in front of [include RatOS/printers/v-core-3/300.cfg] if you have a bigger machine.
#[include RatOS/printers/v-core-3/200.cfg]
#[include RatOS/printers/v-core-3/300.cfg]
[include RatOS/printers/v-core-3/400.cfg]
#[include RatOS/printers/v-core-3/500.cfg]

#############################################################################################################
### HOMING
### Pick your probe and endstops
#############################################################################################################
# BL Touch
#[include RatOS/z-probe/bltouch.cfg]

# Inductive/Capacitive probe
#[include RatOS/z-probe/probe.cfg]

# Euclid probe (please read the RatOS documentation for instructions)
[include RatOS/z-probe/euclid.cfg]

# Klicky probe (please read the RatOS documentation for instructions)
#[include RatOS/z-probe/klicky/klicky.cfg]
#[include RatOS/z-probe/klicky/unklicky.cfg]

# Physical endstop on X
[include RatOS/printers/v-core-3/physical-endstop-x.cfg]
# Physical endstop on Y
[include RatOS/printers/v-core-3/physical-endstop-y.cfg]

# Sensorless homing (Beware: this requires manual tinkering and does not work if your x/y stepper drivers
# have clipped DIAG pins). It is strongly encouraged to use physical endstops if you're a beginner.
# If you still wish to proceed, copy config/templates/sensorless-homing-tmc2209.cfg to the root directory and
# remove the # from the line below, then tune the settings in it, until you have reliable homing.
#[include sensorless-homing-tmc2209.cfg]

# If you want to only run sensorless homing on a single axis, copy the corresponding file from config/templates
# to the root directory and uncomment it below. Then tweak the settings in it until you have reliable homing.
#[include sensorless-x-homing-tmc2209.cfg]
#[include sensorless-y-homing-tmc2209.cfg]

#############################################################################################################
### INPUT SHAPER
### Enable/disable input shaper calibration
#############################################################################################################
# Uncomment this next line if you have an ADXL345 connected to your control board
[include RatOS/printers/v-core-3/input-shaper.cfg]


#############################################################################################################
### TOOLHEAD
### Pick your extruder and hotend
#############################################################################################################
# Extruder
#[include RatOS/extruders/bmg.cfg]
#[include RatOS/extruders/lgx.cfg]
#[include RatOS/extruders/lgx-lite.cfg]
#[include RatOS/extruders/orbiter.cfg]
[include RatOS/extruders/orbiter-1004.cfg] # Use this with the LDO-36STH20-1004AHG motor
#[include RatOS/extruders/hemera.cfg]
#[include RatOS/extruders/titan.cfg]

# Hotend
#[include RatOS/hotends/v6.cfg]
#[include RatOS/hotends/revo.cfg]
#[include RatOS/hotends/dragonfly.cfg]
[include RatOS/hotends/rapido.cfg]
#[include RatOS/hotends/copperhead.cfg]
#[include RatOS/hotends/mosquito.cfg]
#[include RatOS/hotends/mosquito-magnum.cfg]
#[include RatOS/hotends/dragon-standard-flow.cfg]
#[include RatOS/hotends/dragon-high-flow.cfg]


#############################################################################################################
### FANS
### If your board has 4 pin fan headers and you want to use them, you can enable them here.
### NOTE: If none are uncommented, the default 2pin fan headers will be used.
#############################################################################################################
# Part cooling
#[include RatOS/4pin-fans/part-cooling-fan-25khz.cfg]
#[include RatOS/4pin-fans/part-cooling-fan-100hz.cfg]

# Hotend / Toolhead cooling
#[include RatOS/4pin-fans/toolhead-fan-25khz.cfg]
#[include RatOS/4pin-fans/toolhead-fan-100hz.cfg]

# Control board cooling
#[include RatOS/4pin-fans/controller-fan-25khz.cfg]
#[include RatOS/4pin-fans/controller-fan-100hz.cfg]
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

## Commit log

2022-03-04 added some mods
    [Door_Handle_RR_stock_compatible.stl, V-Core-heat-inset_bed_arm_back.step, V-Core-heat-inset_bed_arm_back.stl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]
2022-03-04 added more MBFS mods
    [Dragon_heatsink_support.step, Dragon_heatsink_support.stl, LGX_Lite_face_plate_V5.step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]
2022-03-05 added de_printat
    [10x_cable_clip_30x30.stl, 1xnormal+1xmirrored_lead_screw_motor_cage_front.stl, 2X_face_belt_grabber.stl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]
2022-03-06 replaced the standard RR bedarms with the heat-insert bedarms
    [V-Core-heat-inset_bed_arm_back.stl, V-Core-heat-inset_bed_arm_left.stl, V-Core-heat-inset_bed_arm_right.stl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]
2022-03-06 removed some files
    [DIN_Rail-Endcap.stl, din_rail-holder.stl, din_rail-holder.stp]
2022-03-06 modified din_rail_holder
    [din_rail-holder.stl, din_rail-holder.stp]
2022-03-07 added correct pillow
    [pillow_block_lower.step]
2022-03-07 added motor cage with lips
    [din_rail-holder.prt, lead_screw_motor_cage_back_lip.3mf, lead_screw_motor_cage_back_lip.step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]
2022-03-07 added the Sabre box for Igus Chain
    [sabre_holder.stp, sabre_holder_top.stp, v-core_3_armchainmount_sabre.stp]
2022-03-10 added some extras
    [5x_DIN_Support.stl, 6x_din_rail-holder.stl, DIN_Support_X2.stl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]
2022-03-14 added Din rail end
    [din_rail-end.prt, din_rail-end.stl, din_rail-end.stp]
2022-03-14 added adapter for MeanWell RS-25-5
    [rs-25-5_din_adapter.stl, rs-25-5_din_adapter.stp]
2022-03-15 rearranged and renamed some folders
    [10x_cable_clip_30x30.stl, 1xnormal+1xmirrored_lead_screw_motor_cage_front.stl, 2X_face_belt_grabber.stl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]
2022-03-15 more refactorization
    [2X_face_belt_grabber.stl, 2X_tension_slider_9mm_belt_M5.stl, 3030 Cable Clip.step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]
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2022-03-16 removed door handles
    [Door_Handle_RR_stock_compatible.stl, door_handles.step]
2022-03-18 added carbon tube adapter
    [x-tube_nuts.stl]
2022-03-19 added adapter for Meanwell LRS-200-24
    [lrs-200-24_din_adapter_v3.step, lrs-200-24_din_adapter_v3.stl]
2022-03-31 added SabreBox
    [box.stl, box.stp, box_holder.stl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]
2022-03-31 added EVA Toolboard Holder
    [eva_toolboard_cable_relief v1.stl, eva_toolboard_mount v1.stl]
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2022-05-22 added klipper_config to the repo
    [mainsail.cfg, printer.cfg]
2022-05-31 latest printer.cfg
    [printer.cfg]
2022-05-31 Revert "latest printer.cfg"
    This reverts commit 89daf5a2a76ad21f5101b7880d27c16b47b37538.
    [printer.cfg]
2022-06-05 more views
    [printer.cfg]
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2022-08-22 update after a long time
    [pam.cfg, printer.cfg]
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2022-08-30 added the enclosure
    [3030_handle.stp, back-panel_DIBOND.dxf, back-panel_DIBOND.stp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]
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2022-09-01 updated enclosure
    [back-panel.stp, back-panel_DIBOND.dxf, front-panel.stp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]
2022-09-01 modified side panel
    [side-panel.stp, side-panel_2X_PC4mm.dxf]
2022-09-03 updated the enclosure panels (again)
    [back-panel.stp, front-panel.stp, side-panel.stp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]
2022-09-03 added screw holder for the top panel
    [screw_holder.stp]
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2022-10-22 config backup
    [printer.cfg]
2022-10-22 config backup after adding BTT filament sensor
    [printer.cfg]
2022-10-22 updated z_offset
    [printer.cfg]
2022-11-13 changed on X and Y to TMC5160 Pro drivers at 50V
    [printer.cfg]
2022-11-25 silent steppers and adjusted IS
    [printer.cfg]
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2022-12-02 added documentation on Multi-material printing in SuperSlicer
    [RR_Disk.3mf]
2022-12-02 added my SuperSlicer profiles
    [ratrig-vcore-bed-400x400.stl]
2022-12-15 added kick_start for the [fan] and changed z_offset
    [printer.cfg]
2022-12-18 updated printer.cfg and the SS profile for ASA
    [printer.cfg]
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2023-01-21 added lights
    [pam.cfg, printer.cfg]
2023-02-17 updated MM printing instructions
    [RR_Disk.3mf]
2023-02-27 saved printer.cfg before adding changes to measure gantry deflection
    [printer.cfg]
2023-03-28 switched to RatOS 2.0
    [klipper.cfg, mainsail.cfg, pam.cfg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]
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2023-10-26 upgraded to VCore3.1, EBB36 v1.2, CHC Pro etc.
    [klipper.cfg, mainsail.cfg, priming.cfg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]
2023-11-19 updated SS profiles and printer configuration
    [printer.cfg]
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2024-01-04 snapshot with SuperPinda before replacing it with Euclid
    [printer.cfg, timelapse.cfg]
2024-01-07 changed from SuperPinda to Euclid probe
    [printer.cfg]
2024-01-21 switched from PAM to RR Adaptive Meshing
    [printer.cfg]
2024-03-27 updated printer config and SS profiles
    [klipper.cfg, pam.cfg, printer.cfg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]
2024-06-02 added object exclusion, two enclosure temp sensors and cleaned up a bit printer.cfg
    [printer.cfg]
2024-06-02 cleaned up printer.cfg in the toolboard section
    [printer.cfg]
2024-07-15 update to RatOS v2.1
    [RatOS.cfg, RatOS_modified.cfg, mainsail.cfg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]
2024-07-15 update config names
    [RatOS.cfg, RatOS_modified.cfg, mainsail.cfg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]
2024-07-27 added PTC heater and fixed the electronics fan
    [RatOS.cfg, RatOS_modified.cfg, printer.cfg]
2024-07-29 PTC heater tweaks
    [printer.cfg]
2024-09-09 increased PTC max PWN to 50 percent; some changes due to RatosConfiguration updates
    [RatOS.cfg, RatOS_modified.cfg, klipper.cfg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]
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2024-12-08 Added E-Stop. Increased max power of the chamber heater to 75 percent. Reduced target temp for electronics to 22 degrees
    [printer.cfg, ratos-variables.cfg]
2025-01-02 update to the configurator
    [ratos-variables.cfg]
2025-02-01 added air filter, configured it in the slicer to run at start and stop print
    [RatOS_modified.cfg, printer.cfg]
2025-04-27 updated SuperSlicer and allowed for unsupported slicers
    [printer.cfg]
